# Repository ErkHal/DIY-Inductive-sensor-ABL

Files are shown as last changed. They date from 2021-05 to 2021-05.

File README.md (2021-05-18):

# DIY Inductive sensor ABL
Stupid cheap DIY inductive sensor for auto bed leveling of a 3D Printer.

Reference used while writing these instructions: 
https://www.youtube.com/watch?v=9i5hAhS4QB8

Big thanks to Edward Braiman and his video for guiding me to the right direction !

My version is for my Ender 3 Pro with the SKR V1.4 Turbo mainboard, using a similar but not identical sensor. The wiring seems to be the same though.

This sensor works really well with a spring steel buildplate, I've yet to try with other materials.

This guide assumes you have basic knowledge about compiling Marlin and modifying it, as well as accessing a GCode terminal. If you don't, there are far better teachers than me on YouTube for learning it.

# Making it

Sensor I used with my setup:  
https://www.aliexpress.com/item/1005001622205353.html  
It's a 5v inductive NPN sensor, in an M8-sized housing making it pretty compact but accurate enough.

You need to print out the bracket for the sensor. The 3D Model is in the STL folder. 
Print settings should be tuned for strength, so 3-4 walls and 10%+ infill and .14mm-.2mm layer height.

## Wiring & Installation

I shouldn't have to say this, but POWER DOWN YOUR PRINTER BEFORE DOING THIS !

Disconnect the Z-endstop switch from the mainboard.

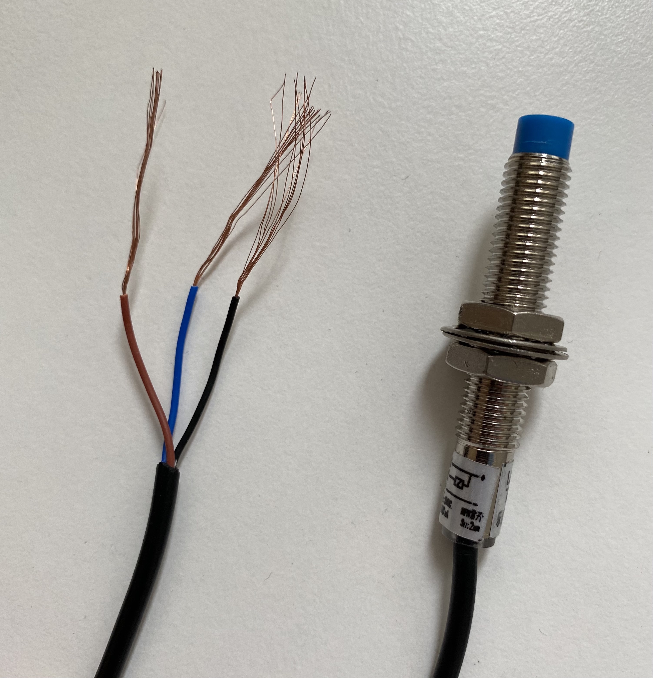
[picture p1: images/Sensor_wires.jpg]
Sensor wires.jpg

Brown = +5V  
Blue = GND  
Black = Signal

Connect these three wires to their corresponding pins in this diagram, so that our sensor replaces the Z-endstop switch:



Mount the 3D-printed bracket (That you _did_ print before disassembling your printer right ???) with stock hardware as shown in the image:

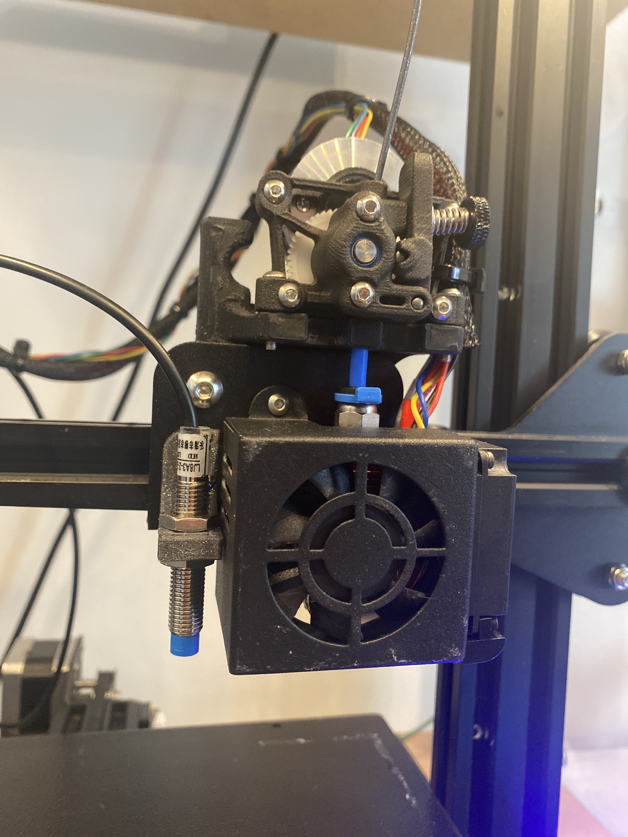
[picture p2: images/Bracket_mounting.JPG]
bracket mounting.jpg


## Firmware

Download the latest marlin, copy-paste your example configs of your printer in there and open up your favorite text editor.

Make these changes to configuration.h:

``` #define Z_MIN_ENDSTOP_INVERTING true  ```  
``` #define Z_MIN_PROBE_ENDSTOP_INVERTING true ```  

Make sure these are uncommented:  
``` #define FIX_MOUNTED_PROBE  ```  
``` #define Z_MIN_PROBE_USES_Z_MIN_ENDSTOP_PIN  ```  
``` #define Z_SAFE_HOMING  ```  
(The reference video states otherwise, however I found out that by uncommenting these it will work as intended)

If you're using the same setup as me, you can add these as probe offsets (these might not be 100% accurate, but good enough):

``` #define NOZZLE_TO_PROBE_OFFSET { -45, -8, 0 } ```  

Remember to also enable your preferred auto bed leveling features !

After configuring other configs regarding your setup, compile and flash your board !
## Testing

Once you've flashed your board, move the X-gantry up and put something metallic under the sensor, it should flash a red LED, indicating that the probe is activated. If not, check wiring.

Now whip up your favorite GCode terminal and connect to your printer.  
Send ``` M119 ``` without anything under the sensor and check that all endstops are in ``` "open" ``` state.  
Place something metallic under it, so that the led lights up. Now send ```M119``` again, and Z-min endstop should be ``` TRIGGERED ```.
If everything works as intended, you can try homing the Z-axis.

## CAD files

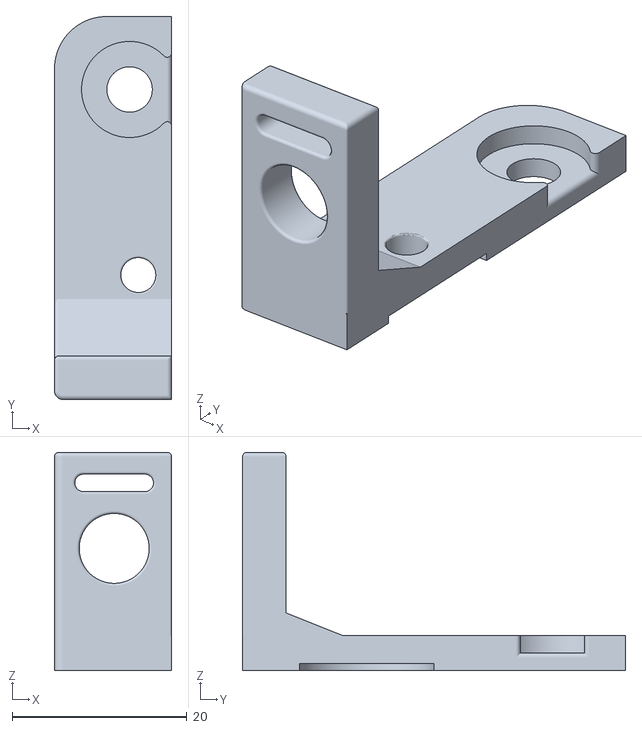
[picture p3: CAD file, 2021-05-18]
STL/Sensor mount.stl
13.4 x 43.9 x 25.0

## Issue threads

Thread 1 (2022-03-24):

PA1 is not +5v tolerant

four0four, 2022-03-24:
So, this is more a design flaw in the BTT board: none of the z-probe pins are five volt tolerant. This would be fine, as these inductive sensors are all open drain (er, collector) (except the PNP ones obviously)...but they have an integrated 10k pull-up, which kinda defeats the purpose.

In other words: the sensor only pulls down to 0v, so we can place a pull-up resistor to whatever voltage level we want for "high". Unfortunately, the sensor has one integrated for whatever reason, so that's not as simple. While you can totally add another transistor or little resistor network to fix this, I just used the PWR-DET header which *is* +5v tolerant (via PC12), so requires none of this. The PWR-DET header doesn't supply power however, so you'll need to add a short jumper to +5v from a neighboring connector (E0-STOP is right there).

You'll unfortunately need to edit `Marlin/src/pins/stm32f1/pins_BTT_SKR_MINI_E3_common.h` to redefine `Z_STOP_PIN` to PC12, as well as `POWER_LOSS_PIN` to -1. I'm not familiar with this codebase, so there may be a more ergonomic way of overriding this via Configuration.h.

Feel free to close this issue, I just wanted to attach this information to the most accurate guide I found :)

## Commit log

2021-05-18 Add mount 3D model
    [Sensor mount.stl]
2021-05-18 Add better sensor mount
    [Sensor mount.stl]
